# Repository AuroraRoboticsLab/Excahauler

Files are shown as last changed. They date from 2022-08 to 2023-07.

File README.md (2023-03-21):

# Excahauler Mining Robot

OpenSCAD source code for building a large autonomous mining robot.  Uses a combination of welded and 3D printed parts.

To build this source code, download OpenSCAD 2020 or newer, and:
```
    git clone https://github.com/AuroraRoboticsLab/AuroraSCAD
    openscad Excahaul_latest.scad
```

The subdirectories contain a variety of subassemblies which are primarily 3D printed, held onto a frame which is primarily welded steel. 

## Parts of the Robot
This is a side view of the entire robot, in Excahaul_latest.scad, holding the rockgrinder tool.
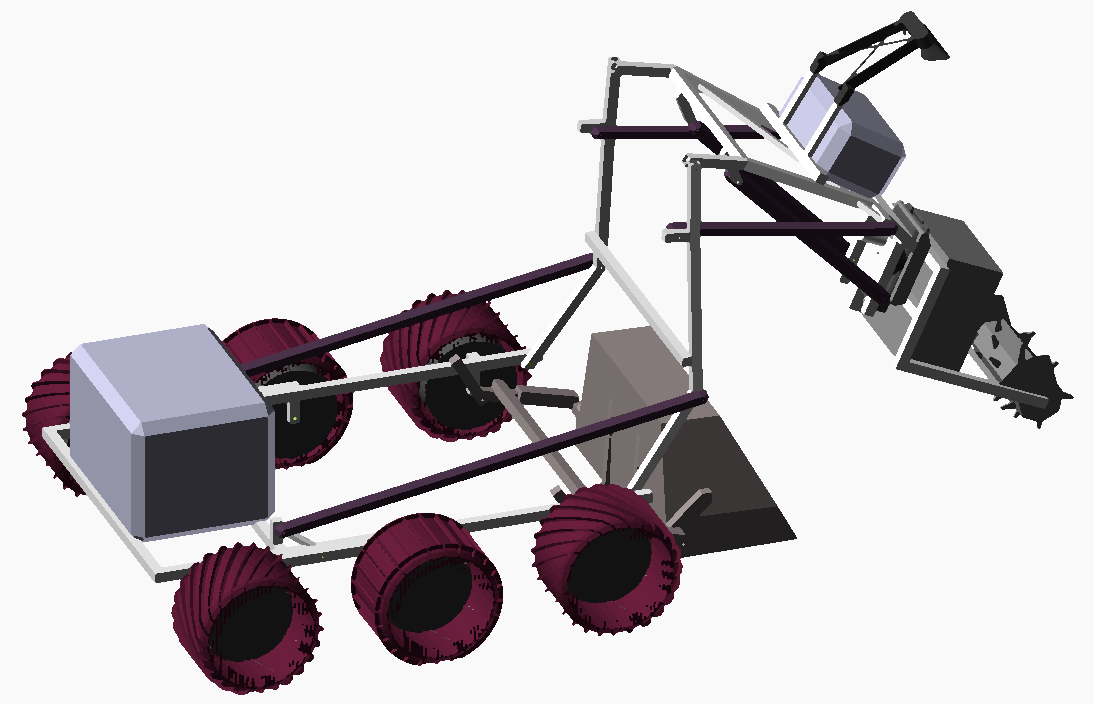
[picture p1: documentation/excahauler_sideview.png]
CAD overview of robot: frame at the bottom, large arm reaching forward, mining tool on front. Overview of the robot


The overall coordinate system has +Y forward (as required by Unity for simulation), +X to the robot's right, and +Z up. This is right handed.

The base of the robot is the welded steel **frame**, which is MIG welded from 1 inch / 25mm steel box tubing like most of the robot's fabricated parts.  The front wheels bolt directly to the frame for stability, and the middle and rear wheels are on a rocker to conform to the ground. The large rear electronics box also bolts on directly, and the front fork and arm boom are bolted directly on the frame as well.
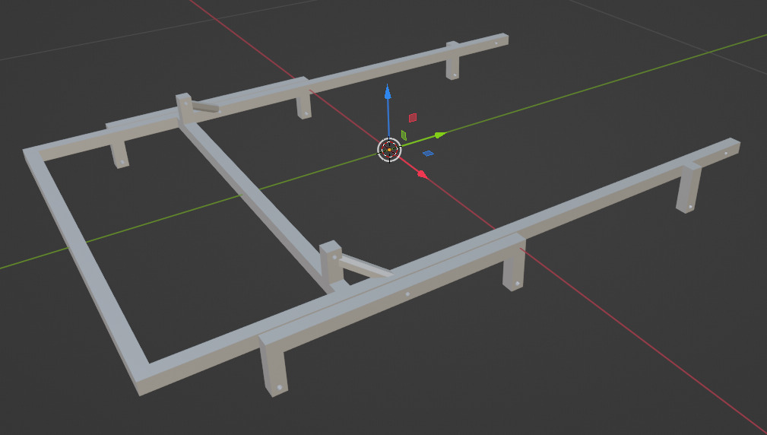
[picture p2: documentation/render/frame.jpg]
Diagram of main robot frame: sparse steel tubes in a rough U shape. Frame: holds the wheels and everything else.


The robot arm moves via two links.  The arm **boom** connects to the robot frame and provides front-back motion. (The boom coordinate system is aligned with the inertial measurement unit mounted on the shorter angled bar, which is rotated about 25 degrees from the longer bar.)
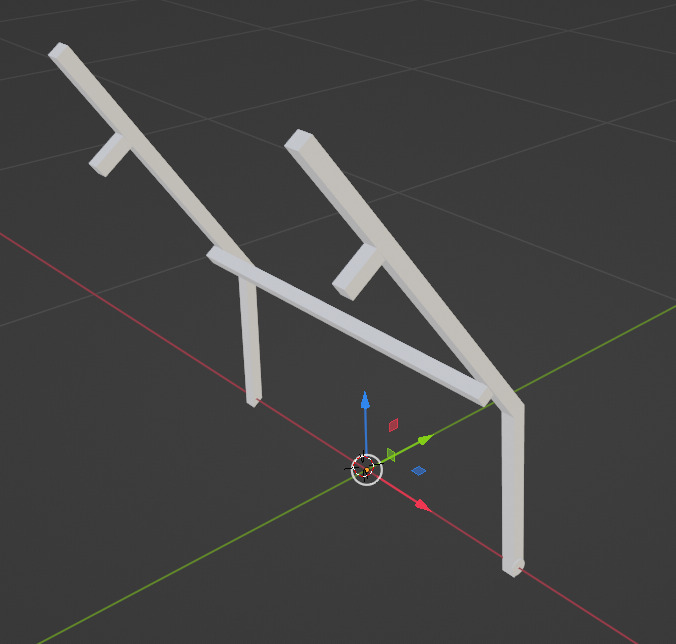
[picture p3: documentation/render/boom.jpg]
Diagram of boom. Boom


The second robot arm link is the **stick** (following the odd excavator naming convention).  The stick has an Intel RealSense D455 depth camera mounted on top, and small electronics box for motor controllers and interfacing.
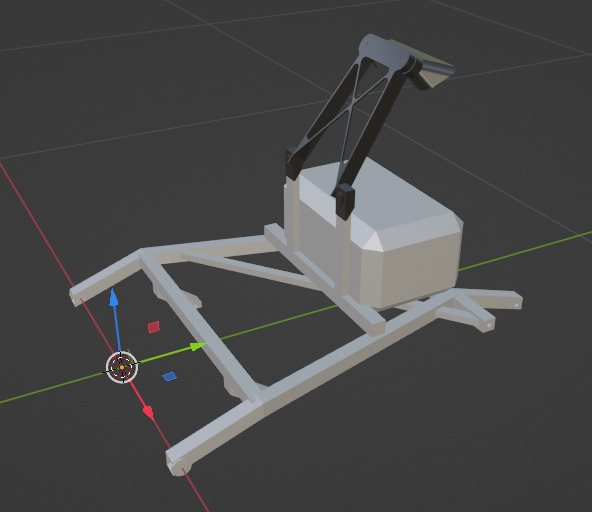
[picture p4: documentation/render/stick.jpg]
Diagram of stick. Stick


The next link holds the tool coupler. It can **tilt** the tool forward and backward via linear actuators, and **spin** the tool via a stepped planetary geartrain. 
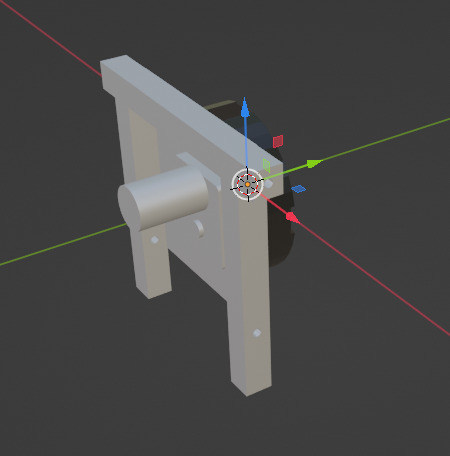
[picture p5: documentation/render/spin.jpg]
Diagram of tilt and spin links. Tilt front-back (YZ) and spin (around Y)


The tool coupler lets us pick up tools using a 2-pin approach similar to excavator quick-change.  The origin is centered on the top pin.  The bottom pin can be locked in place with a rather complex linkage wedged inside.
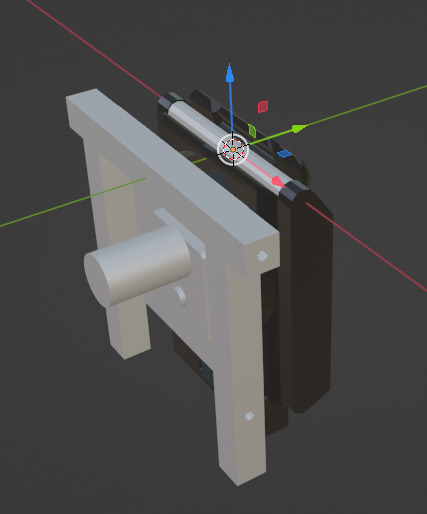
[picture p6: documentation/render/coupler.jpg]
Diagram of coupler. Coupler top pin shown


A variety of excavation **tool**s could be used, but the highest productivity tool is a rock grinder, which spins a drum to mill material directly into the front scoop.  The large ammo can stores the batteries, motor controller, and has space for cooling oil as well.
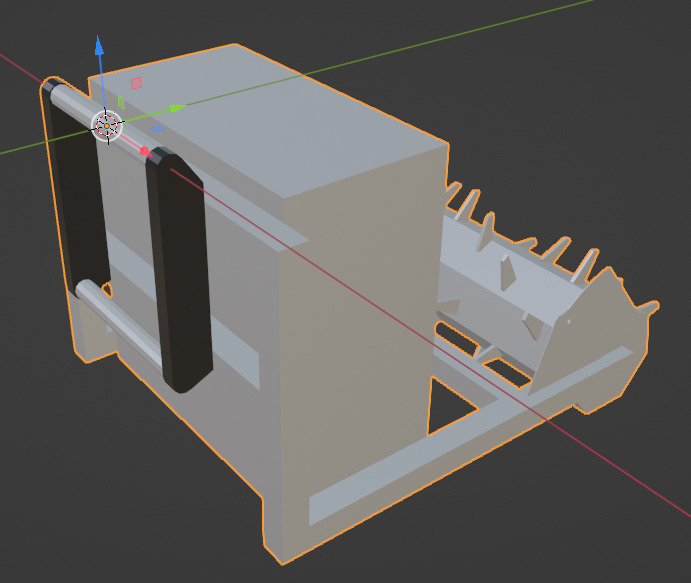
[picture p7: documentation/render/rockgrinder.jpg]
Diagram of rock grinder. Rock grinder tool


We move excavated material around in the front scoop.  The **fork** linear actuator raises and lowers the scoop relative to the frame via this part; the **dump** linear actuator rides on the fork and pivots the scoop to unload material.
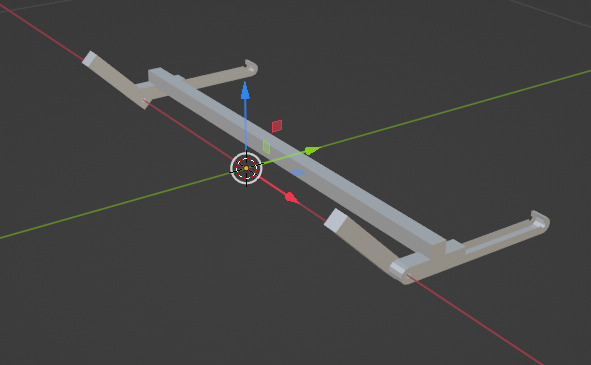
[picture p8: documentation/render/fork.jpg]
Diagram of fork. Fork


The front **scoop** has a volume of 50 liters, which lets it carry a payload of about 50 kg of broken-up regolith simulant chips.  The coordinate system is rotated by 45 degrees to match the inertial measurement unit on the pivot arm. 
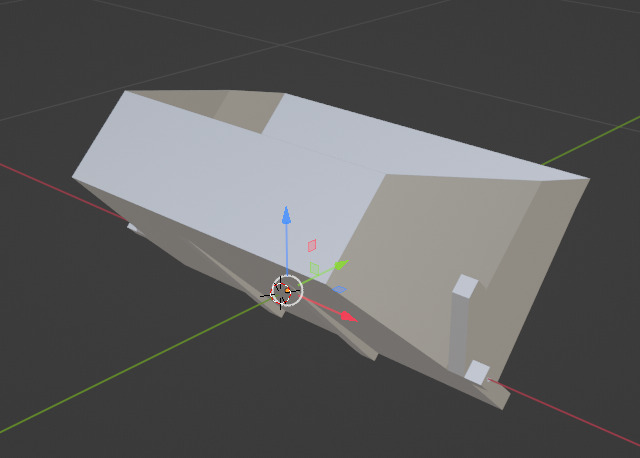
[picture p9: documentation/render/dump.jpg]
Diagram of scoop. Scoop


This is a photo from the front of the robot, showing our first rough physical prototype.
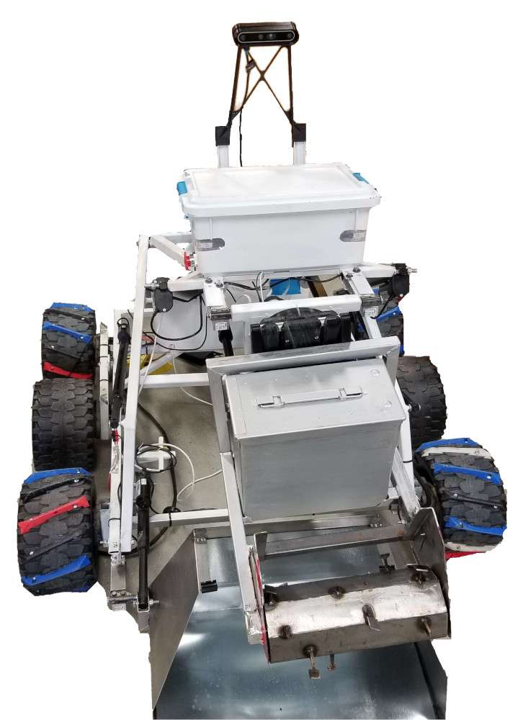
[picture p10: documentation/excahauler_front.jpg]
Photo of robot holding tool. Front view of the robot


Each OpenSCAD file has some comments, but we are adding comments and README to make this easier to follow.  Please contact lawlor@alaska.edu if you have questions or suggestions!

Unless marked otherwise, these source code files are released to the public domain.

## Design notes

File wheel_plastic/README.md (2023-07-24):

Parts to work with blow-molded plastic wheels. 

This wheel style was common on a variety of kid's electric Jeep models circa 2010. 
Part number is B7659-2459 and has four raised drive lugs on the back side, and a simple cone
on the front side.

	https://www.kidswheels.com/parts/wheels-tires/product/522761-power-wheels-jeep-wheel-b7659-2459
	https://www.bettervac.com/Power-Wheels-B7659-2459-Jeep-Wrangler-Barbie-Jeep-Tire

The tires are blow molded from HDPE, so they can be hot-air welded.

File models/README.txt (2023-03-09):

The script "to_stl.sh" converts these .scad files into .stl files, measured in meters,
suitable for importing into Blender or another renderer.

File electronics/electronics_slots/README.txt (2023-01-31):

Basic idea: instead of one big monolithic Arduino, we have dedicated motor controller micros, in their own 3D-printed cases.  E.g., one left side, one right side, one for mining head.

+ Use simpler, more reliable parts (spare electronics possible)
+ Less wire crossing the robot
- More parts to build

-------------------
Standard electronics slot microcontroller is an Arduino Nano 328P with a CH-341 USB serial.

Daniel Kling's 5-pin breakout board:

const unsigned char breakoutPins[6]={ 11,10,9,8,A0,12 };

Arduino Nano  Motor Control Board
D11           [0] signal pin
D10           [1] signal pin
D9            [2] signal pin
D8            [3] signal pin
A0            [4] signal pin?
D12           [5] signal pin

5V             V+  (requires jumper soldered on Nano board)
Gnd            Gnd

Motor drivers, UN178 green brushed boards:

un178_motor_single_t hardware_motor[NANOSLOT_COMMAND_MY::n_motors]={
    un178_motor_single_t(11,12,A0),
    un178_motor_single_t(10,9,8),
    un178_motor_single_t(3,2,4),
    un178_motor_single_t(6,5,7),
  };

----------------
UN178 motor controller x2, each doing 2 motors (4 total motors)

	2x PWM inputs, one each for A and B motors
	4x digital inputs for A and B sides
	gnd in

3-pin encoder inputs (6 copies, including Arduino I2C lines).  Servo 3-pin cables: gnd, 5v, encoder
	1 per controlled motor
	Plus 2 spares: redundant encoders, bag up/down, etc.

With short jumpers, 121ohm current limiters, and 2Kohm pull-up resistors, analog pins read:
  dn 1022-1023 when open
  dn 16-17 when shorted to ground
Probably a dn threshold of 200 or higher would be about right.

RJ-45 serial uplink to main controller: 5v (orange), ground (orange-white), tx0 (brown), rx0 (green)

Nano PWM-capable pins: 3, 5, 6, 9, 10, 11

m[0] LA motor: dir 12(green),A0(red)  PWM 11
m[1] LB motor: dir 9(green),8(red)   PWM 10   (both 490Hz)

m[2] RA motor: dir 2(green),4(red)  PWM 3    (normal 490Hz pin)
m[3] RB motor: dir 5(green),7(red)  PWM 6    (the fast 980Hz pin)

With two UN178's plugged in, current draw is 0.07-0.15A at 12VDC side.

If we target a 500Hz motor update, we have 2ms per cycle.
At 115200 baud, we should be pushing 10KB/sec, or 10 bytes/ms.
So blipping out an A-packet with 6 byte-long encoder counts is probably fine.

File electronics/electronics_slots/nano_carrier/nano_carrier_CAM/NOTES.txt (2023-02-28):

Pass 01: holes, 20 degree cutter, copper side down.  Zero at top left (Y in file are all negative.)
Pass 02: isolate traces, 0.8mm diameter endmill, copper side up.  Zero at bottom left (re-zero Y.)
Pass 03: cut outline of board, 3mm diameter endmill (V works well).

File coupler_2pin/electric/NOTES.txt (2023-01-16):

Desired features:
	- Dust tolerant
		- Built around existing robust connectors, like Anderson power poles?
		- Orient connectors vertically, so dust falls out.
	- Ideally androgynous, to allow:
		- Tool-to-robot
		- Robot-to-charger
		- Tool-to-charger
		- Robot-to-robot
	- High power, up to kW at 28VDC to allow 1C charging of a 1kWh robot or tool battery. 
		- 1 kW / 28 VDC = 35 amps sustained
		- Use 45A rated Anderson power poles

Electrically, I should have:
	Alignment pins
	Heavy amp connection for tools / battery recharge
		Maybe 75A Andersons?
	I2C digital comms: gnd, 5v, SDA, SCL
		Maybe as Andersons, for mech robustness?

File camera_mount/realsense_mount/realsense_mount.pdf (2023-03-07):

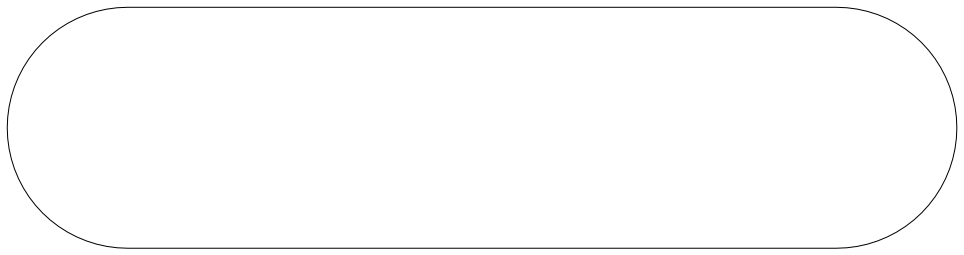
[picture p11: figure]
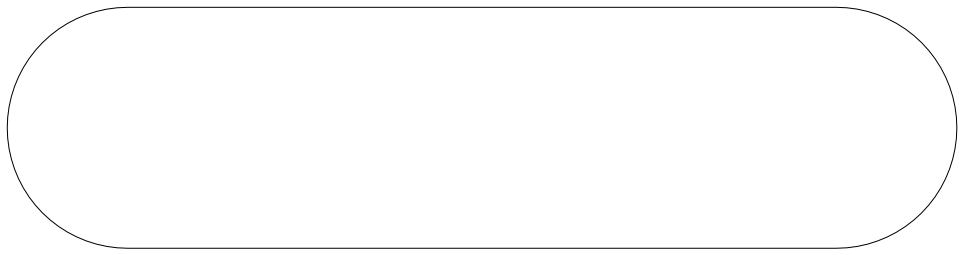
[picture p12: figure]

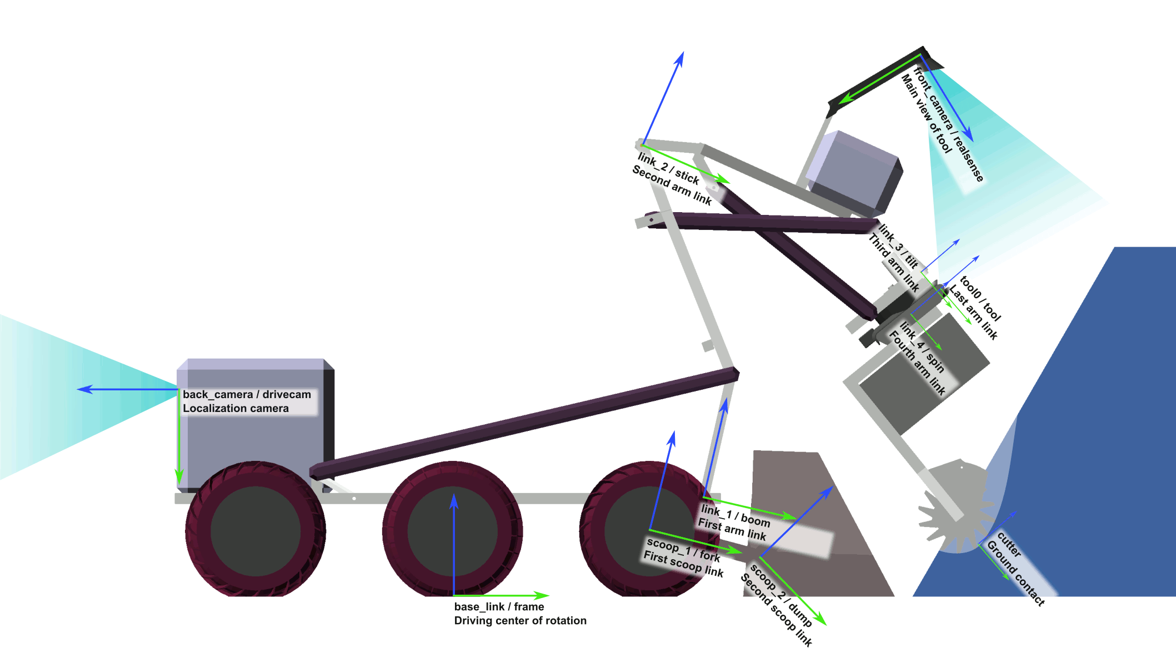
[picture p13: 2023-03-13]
documentation/kinematics/sideview_axes.png

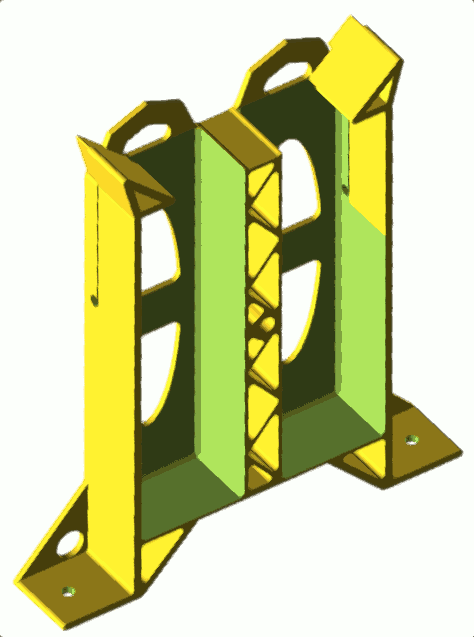
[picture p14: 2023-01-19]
electronics/electronics_slots/driver_slots.png

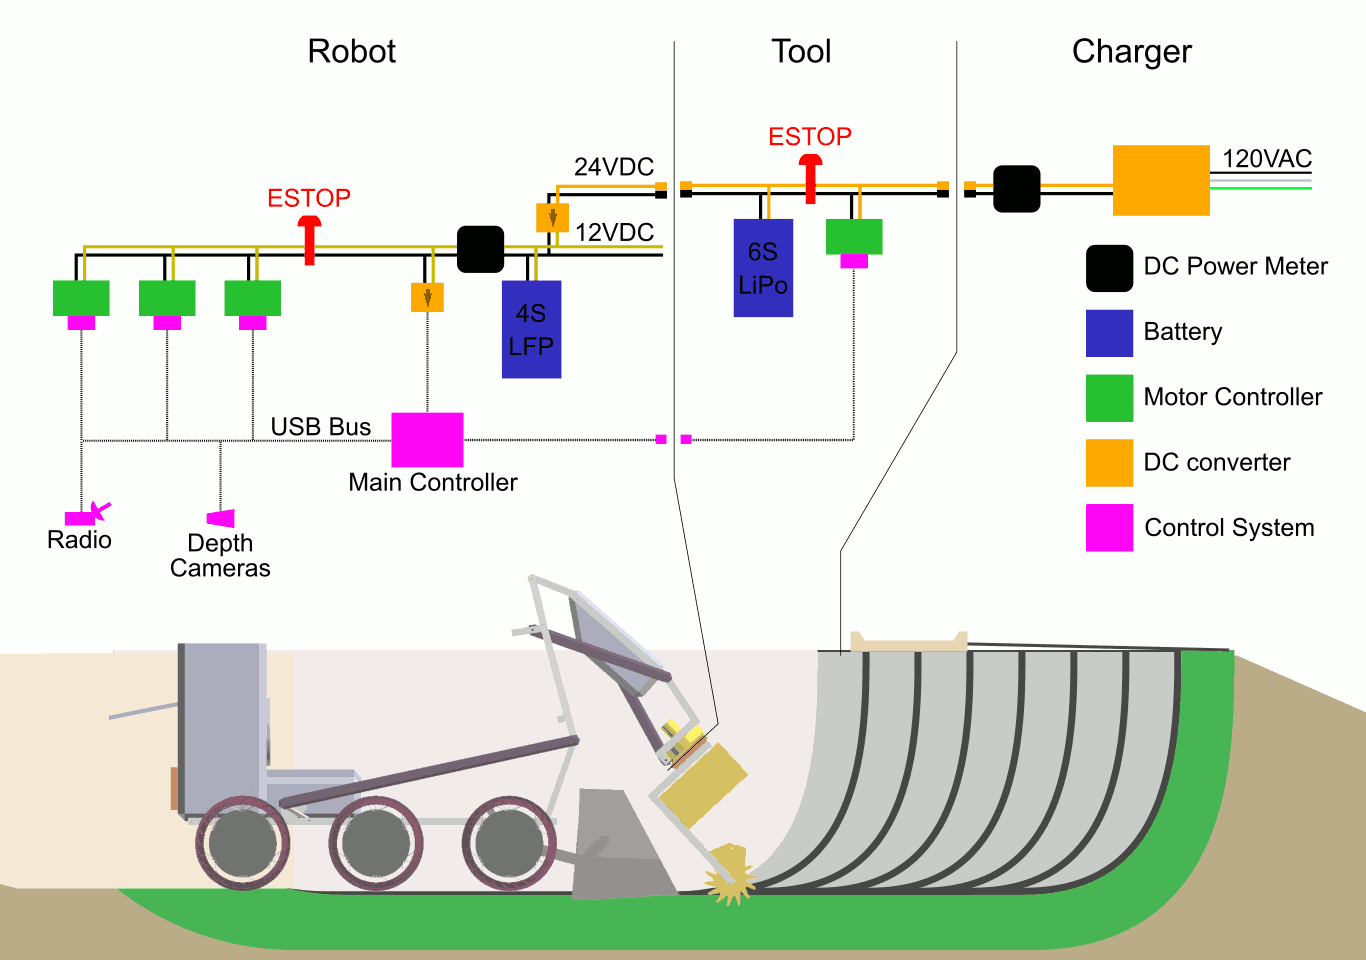
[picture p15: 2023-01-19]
electronics/electrical_architecture.png

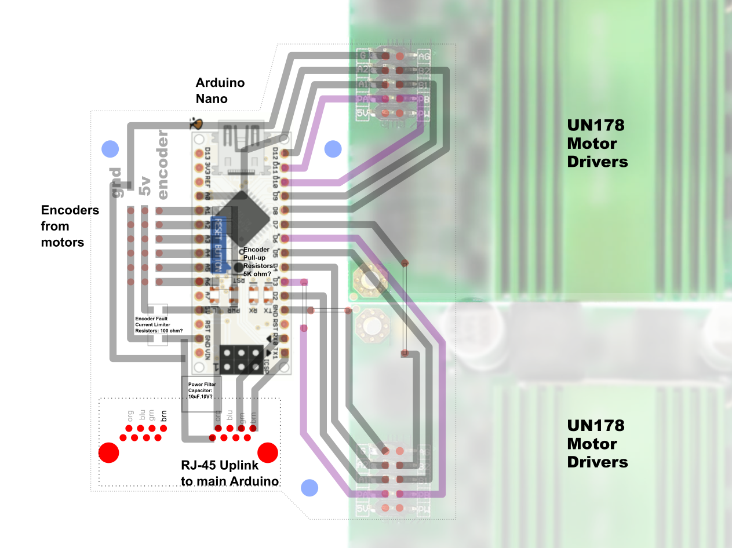
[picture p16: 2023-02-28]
electronics/electronics_slots/nano_carrier/nano_carrier_pinout.png

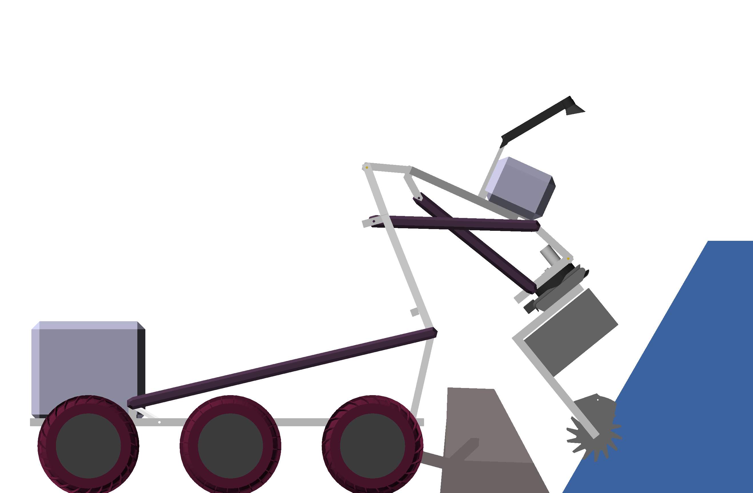
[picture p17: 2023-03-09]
documentation/kinematics/sideview.png

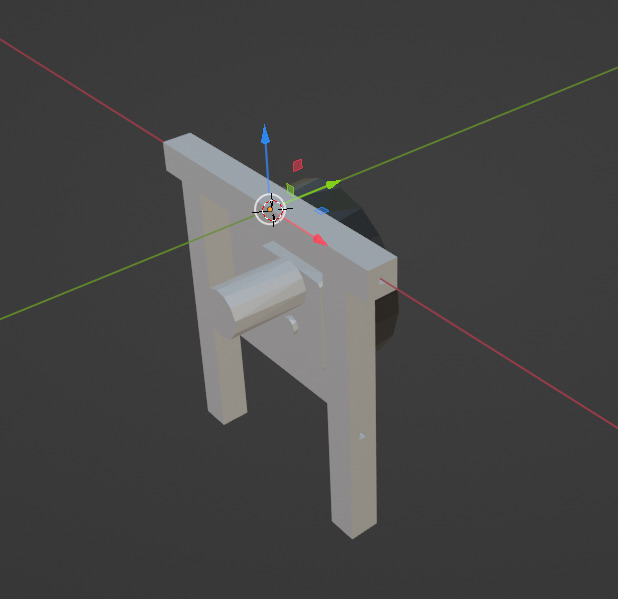
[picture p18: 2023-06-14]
documentation/render/tilt.jpg

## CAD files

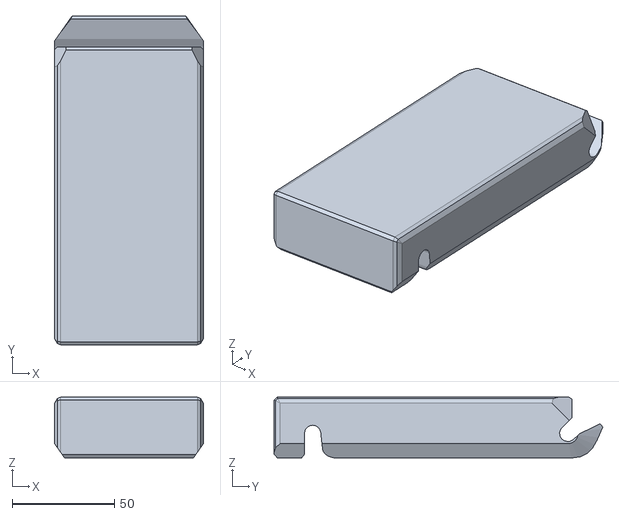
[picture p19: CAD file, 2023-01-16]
coupler_2pin/18mm_coupler/coupler_2pin_solid.stl
73.0 x 161.1 x 29.8

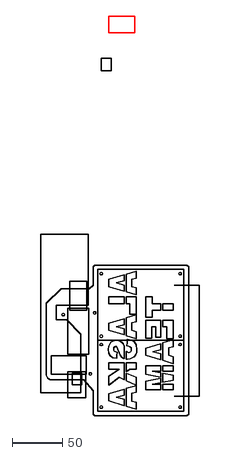
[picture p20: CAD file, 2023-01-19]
electronics/electronics_slots/driver_case_v2_xport.dxf
157.0 x 396.3

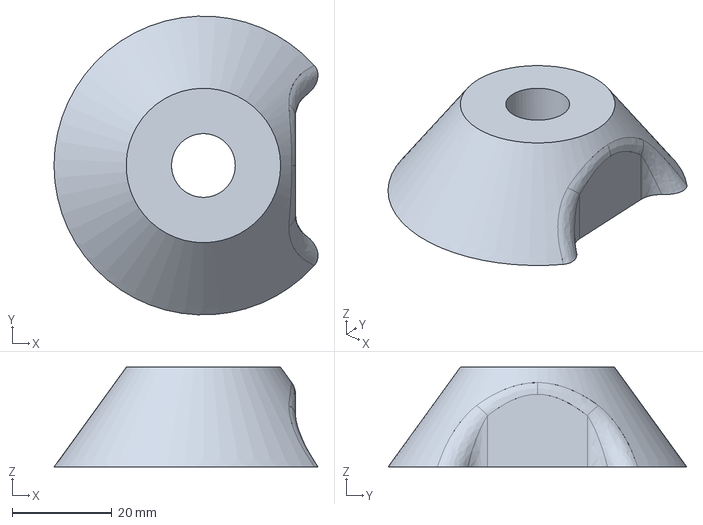
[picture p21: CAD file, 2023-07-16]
wheel_plastic/centercone_v2.iges
53.0 x 60.0 x 20.0 mm

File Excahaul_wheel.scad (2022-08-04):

/*
 Excahauler rigid-caracass wheels.
   This file is included by Excahaul_latest.scad, and for various wheel prototypes.
 
*/

// Wheels
wheelDia=300; // diameter of wheels (less grousers)
wheelRad=wheelDia/2;
wheelThick=200; // thickness of wheels along axles
wheelWall=3.0; // thickness of wheel cylinder material
wheelBevel=15; // corners of wheels beveled for turning
ngrouser=24;  // grouser count from (Intosume et al, 2019)
grouserHt=0.075*wheelDia/2; // height = 7.5% of wheel radius
grouserSize=2.8; // thickness of grousers

// Basic wheel outline, including bevel
module wheelBasicOutline(extraR=0) {

        translate([0,0,wheelThick/2])
            hull() {
                cylinder(d=wheelDia+2*extraR,h=wheelThick-2*wheelBevel,center=true);
                cylinder(d=wheelDia+2.15*extraR-0.6*wheelBevel,h=wheelThick-1.0*wheelBevel,center=true);
                cylinder(d=wheelDia+2.3*extraR-2*wheelBevel,h=wheelThick-0.02*extraR,center=true);
            }
}

// Wheel outline, including bevel and middle hole in spokes
module wheelOutline(extraR=0) {
    difference() {
        wheelBasicOutline(extraR);
        
        translate([0,0,75-extraR])
            cylinder(d1=50,d2=wheelDia,h=wheelThick);
    }
}

module wheelRim() {
    difference() {
        wheelOutline();
        wheelOutline(-wheelWall);
    }
}

// Grousers add traction to wheels
module wheelGrousers(twist=0) 
{
    intersection() {
        difference() {
            wheelOutline(grouserHt);
            wheelOutline(-0.5);
        }
        union() {
            r=wheelDia/2+grouserHt;
            startR=wheelDia/4;
            twistRate=360.0/1400.0; // degrees of grouser twist per mm of wheel height
            
            translate([0,0,wheelThick/2])
            for (bevel=[1])
            {
                h=wheelThick-2*wheelBevel*bevel;
                twistDeg=twist*h*twistRate;
                rotate([0,0,-bevel*wheelBevel*twistRate]) //<- line up two sections
                linear_extrude(twist=twistDeg,slices=twist?4:0,height=h,convexity=8,center=true)
                {
                    for (grouser=[0:360/ngrouser:360-1])
                        rotate([0,0,grouser])
                        if (bevel) // bevel the grouser root
                            translate([wheelDia/2-0.2,0,0])
                                rotate([0,0,45])
                                {
                                    s=7; // bevel this far
                                    square([s,s],center=true);
                                }
                        else // plain grouser:
                            translate([startR,-grouserSize/2,0])
                                square([r-startR,grouserSize]);
                }
            }
            
            // Straight planar grousers (instead of helix above)
            for (grouser=[0:360/ngrouser:360-1])
                rotate([0,0,grouser+(twist?4.4:-4.1)])
                    translate([wheelDia/2,0,wheelThick/2])
                        rotate([twist*33.5,0,0]) //<- fixme: somehow related to twistRate
                            cube([100,grouserSize,2*wheelThick],center=true);
            
            if (twist==0) // ring stiffener / cross-slip preventer rings on middle wheels
                for (z=[wheelBevel+grouserSize/2,wheelThick-wheelBevel-grouserSize/2])
                translate([0,0,z])
                    cylinder(h=grouserSize,r=r,center=true);
            /*
            translate([0,0,wheelThick/2])
                for (grouser=[0:360/ngrouser:360-1])
                    rotate([0,0,grouser])
                    {
                        // Big blocks on outside of wheels
                        translate([wheelDia/2,0,0])
                            cube([2*grouserSize,grouserSize,wheelThick],center=true);
                        
                        // Small ribs on inside
                        rotate([5,0,0])
                        //translate([0,grouserSize/2,0])
                            cube([wheelDia-2*wheelBevel,2,wheelThick],center=true);
                    }
            */
        }
    }
}

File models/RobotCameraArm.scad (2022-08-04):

$subpart=1;
include <../Excahaul_latest.scad>;
scale(0.001) {
    translate(-cameraPivot) cameraArm(0);
    cameraArmDisk();
}

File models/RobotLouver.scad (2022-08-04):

$subpart=1;
include <../Excahaul_latest.scad>;
scale(0.001) radiatorLouver(0.0);

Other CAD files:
models/Wheel.scad
CAM/Boom_CAM.scad
CAM/Frame_CAM.scad
CAM/ScoopDrawings.scad
CAM/Stick_CAM.scad
CAM/Stick_projector.scad
Excahaul_latest.scad
camera_mount/camera_mast_mount.scad
camera_mount/camera_standring.scad
camera_mount/realsense_mount/realsense_mount.scad
coupler_2pin/18mm_coupler/18mm_coupler.scad
coupler_2pin/18mm_coupler/sideplates.scad
coupler_2pin/18mm_coupler/sideplates_charger.scad
coupler_2pin/8mm_mini_coupler/coupler_2pin_latest.scad
coupler_2pin/electric/electric_coupler.scad
coupler_2pin/lockbar/lockbar_gearbox.scad
coupler_2pin/lockbar_gearbox.scad
coupler_2pin/tool_coupler_interface.scad
electronics/electronics_slots/driver_case_interface.scad
electronics/electronics_slots/driver_case_v2.scad
electronics/electronics_slots/driver_slots.scad
electronics/electronics_slots/pi_slot/pi_slot.scad
electronics/manual_controller/control_pendant.scad
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

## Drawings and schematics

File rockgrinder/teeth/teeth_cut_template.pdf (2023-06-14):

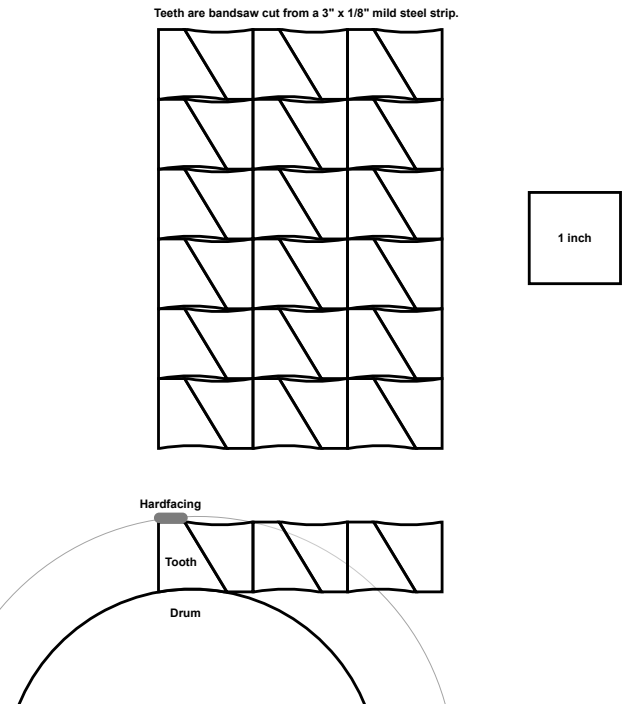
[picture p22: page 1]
1 inch; Drum; Tooth; Hardfacing

Teeth are bandsaw cut from a 3" x 1/8" mild steel strip.

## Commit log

2022-08-04 Getting CAD/CAM source code into version control. These have been developed for up to 18 months now.
    [ArmBoom.scad, ArmStick.scad, CouplerArm.scad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]
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2022-10-14 Switch to a regular box model for the front scoop.
    [Excahaul_latest.scad]
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2022-10-16 Avoid depth fighting on wheel spokes, by shrinking intersecting wheel.
    [Excahaul_latest.scad]
2022-11-04 Update front scoop bucket with reinforcing steel frame (as-built).
    [Excahaul_latest.scad, ScoopBox.scad, ScoopDrawings.scad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]
2022-11-04 Add teeth to the rock grinder tool model, and trim back the tool scoop.
    [robot_rockgrinder.scad, rockgrinder.scad]
2023-01-16 Added 18mm version of tool coupler, with 150mm wide by 175mm between pins. This leaves enough space for an electric coupler with power and USB connections.
    [18mm_coupler.scad, coupler_2pin_latest.scad, coupler_2pin_solid.stl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]
2023-01-16 Add 2021 design for stepped planetary gear reducer. This spams planets for better holding torque.
    [gear_library.scad, geared_coupler.scad]
2023-01-16 Replace old gear_library with AuroraSCAD standardized version (divide pitch by pi is only real change).
    [gear_library.scad, geared_coupler.scad]
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2023-01-19 Prototype electronics slots, with removable cases storing up to two UN178 motor drivers.
    [driver_case_interface.scad, driver_case_v2.scad, driver_case_v2_xport.dxf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]
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2023-02-02 Bracket for mounting MPU-6050 board onto a 1" steel tube frame of the robot using 2x M3 screws.
    [mpu_mount_bracket.scad]
2023-02-04 Initial version of sideplates that hold electrical metallic tubing (EMT) pins for the tool coupler to grab. These parts are bolted to the mining head.
    [sideplates.scad]
2023-02-04 Revised dimensions of EMT hole, and close off top for strength.
    [sideplates.scad]
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2023-03-07 Version 3 of RealSense D455 mounting bracket. This bolts onto two uprights welded onto the stick.
    [realsense_mount.scad]
2023-03-09 Updated Excahauler model with new tool coupler and realsense camera mast.
    [18mm_coupler.scad, Excahaul_latest.scad, bevel.scad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]
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2023-03-09 Add STL model sfor rock grinder, and make front scoop terminology more consistent (fork, dump, etc.)
    [Excahaul_latest.scad, Rockgrinder.scad, ScoopFork.scad]
2023-03-09 Fixing 3D model coordinate systems.
    [ArmStick.scad, Excahaul_latest.scad, PlowFrame.scad]
2023-03-09 Reworked coordinate systems for tool to be more sane (Z+ up instead of Y- up!).
    [18mm_coupler.scad, Excahaul_latest.scad, ScoopDrawings.scad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]
2023-03-09 Added photos and renders of finished robot, mostly linked from top level README.
    [Boom_CAM.scad, Excahaul_latest.scad, Frame_CAM.scad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]
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2023-03-09 Added high resolution side view, with annotated axes.
    [Excahaul_latest.scad]
2023-03-11 Tuned geometry to match as-built robot (for kinematic model)
    [Excahaul_latest.scad]
2023-03-12 Add simple 3D models in OBJ, DAE, and Blender formats. These are from the OpenSCAD with hollow=0 and $FEMmode=1 for simpler geometry, plus hand cleaning for small high-performance models.
    [ArmBoom.scad, ArmStick.scad, Excahaul_latest.scad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]
2023-03-13 Switch wheel model to triangles instead of quads and higher polyhedra.
    [Excahaul_simple_2023.blend]
2023-03-13 Fix coordinate system for frame (Z==0 should be the ground) and tilt (origin should be at stick pivot point).
    [Excahaul_simple_2023.blend]
2023-03-13 Reorient boom so at zero rotation, the first part is straight up instead of forward (matches IMU as-built, simpler coordinate system).
    [Excahaul_simple_2023.blend, boom.scad]
2023-03-18 Update part coordinate system axes to match kinematic model and prototype.
    [Excahaul_latest.scad, Excahaul_simple_2023.blend, rockgrinder_frame.scad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]
2023-03-21 Update boom and dump render JPG files to match as-built coordinate system.
    [Excahaul_latest.scad]
2023-03-28 Add blow-molded Barbie Jeep wheel mount parts. Initial work on carrier bearing.
    [centercone_v2.stl, centercone_v3.scad, gearwave.scad]
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2023-04-29 Parts for machining Peg Perego gearbox gears--these need metal bushings added.
    [gear_holders.scad, gearbox_dimensions.xls]
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2023-05-23 Use thinner bearings, to save weight, and allow smaller 4" ID steel drum.
    [rockgrinder.scad]
2023-05-23 Add abbreviated version of tool coupler to go on bottom of rock grinder for charging.
    [18mm_coupler.scad, sideplates_charger.scad]
2023-05-23 Add pi slot, to hold Raspberry Pi (via zip ties) in standard driver slot.
    [driver_case_interface.scad, driver_case_v2.scad, pi_slot.scad]
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2023-05-23 Hold a gear for machining on a lathe 3-jaw chuck. We drill these out to 10mm to press-fit bushings.
    [gear_holders.scad]
2023-06-14 Fix collision between motor gears and drum housing in two ways: smaller motor gears, and back to flat plate drum.
    [rockgrinder.scad]
2023-06-14 Updates for mounting a mini coupler on the charger, to charge the tool (and then robot).
    [18mm_coupler.scad, Excahaul_simple_2023.blend, driver_case_interface.scad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]
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2023-07-01 Version 3: works, and lightweight, though still extremely loud and pulls 30+ watts at idle (vs conventional geartrain's 15ish watts).
    [gearwave.scad]
2023-07-10 Dialing in 3D printable replacement gears for Peg Perego gearbox.
    [gear_holders.scad, gear_replacement.scad, gearbox_dimensions.xls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]
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2023-07-16 Slightly modify gear modulus to match real gears better.
    [geartype_perego.scad]
2023-07-16 Add PolyGear option for true involute gear shape.
    [gear_replacement.scad]
2023-07-22 Updated sun gear to have a little extra height, so it doesn't get pushed forward and shear off.
    [rockgrinder.scad]
2023-07-23 Move polygear call to new adapter library (adapted from this code).
    [gear_replacement.scad]
2023-07-23 New coarser output gear pitch will hopefully reduce gear breakage. (Gear reduction drops from 31:1 to 28:1 though.)
    [rockgrinder.scad]
2023-07-24 Straight-sided gears, to avoid work of inserting bushings for short-lived gears.
    [rockgrinder.scad]
2023-07-24 Move 3D printed tire grousers (old style) to wheel_plastic/printed_grousers/
    [Excahaul_latest.scad, centercone_v2.iges, centercone_v2.stl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]
2023-07-25 Updated top cap design (original melted!) to reduce curl in nylon print.
    [rockgrinder.scad]
2023-07-29 Use 10mm OD x 8mm ID bushings in rockgrinder gears, for better wear properties (this version on robot, has worked for hours).
    [rockgrinder.scad]
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
